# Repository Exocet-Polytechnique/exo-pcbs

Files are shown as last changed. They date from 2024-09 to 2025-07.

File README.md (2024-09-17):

# exo-pcbs
KiCad projects for our electrical control unit PCBs

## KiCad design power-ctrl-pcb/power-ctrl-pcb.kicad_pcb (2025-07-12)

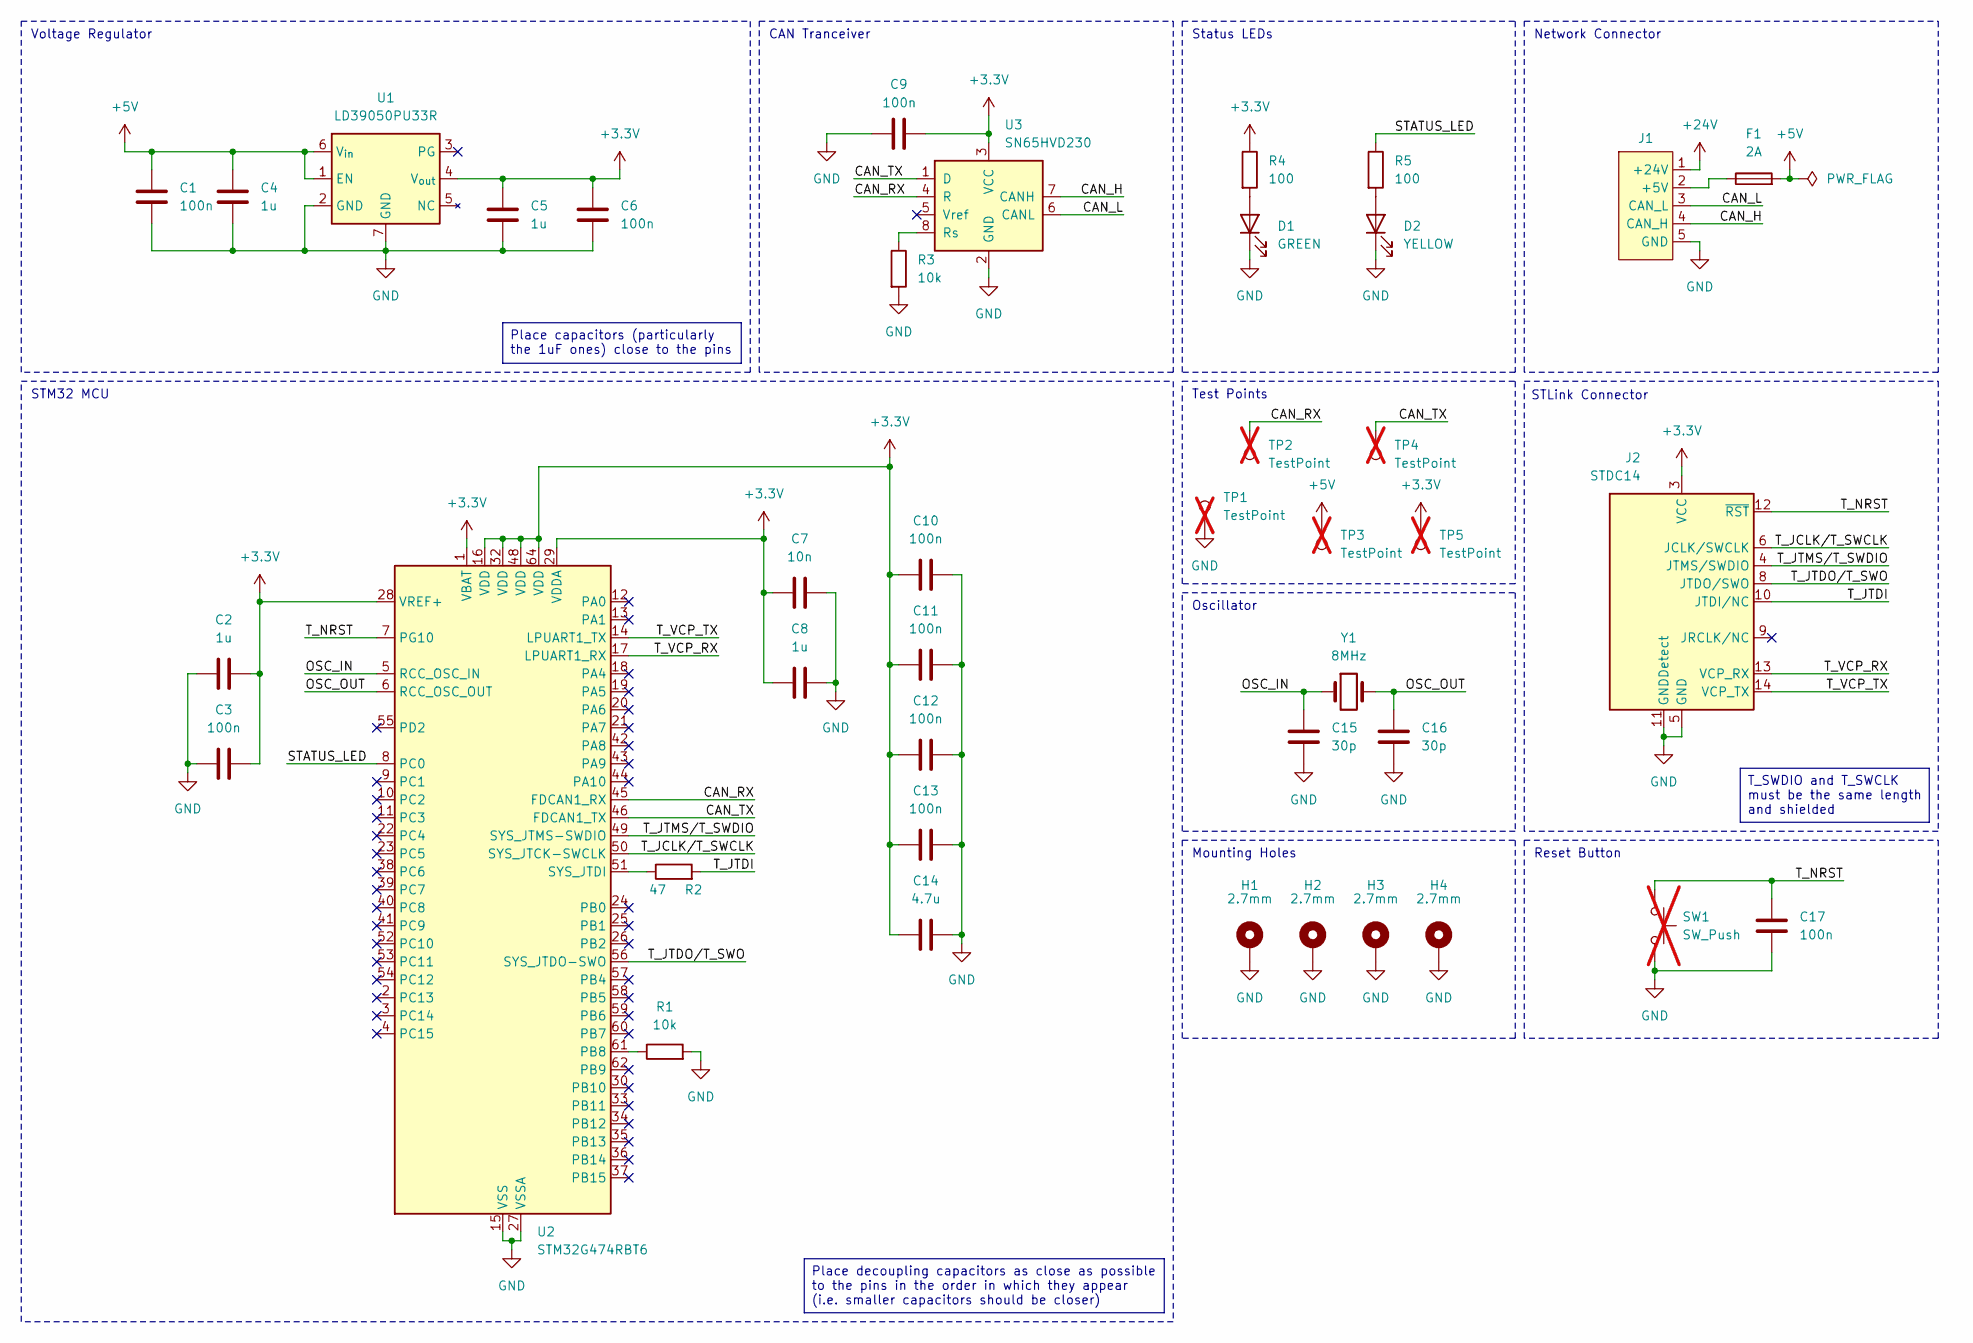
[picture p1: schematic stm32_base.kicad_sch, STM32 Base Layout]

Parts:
C1, C3, C6, C9, C10, C11, C12, C13, C17: 100n; C_0402_1005Metric; JLCPCB C1525
C2, C4, C5, C8: 1u; C_0402_1005Metric; JLCPCB C52923
C7: 10n; C_0402_1005Metric; JLCPCB C15195
C14: 4.7u; C_0402_1005Metric; JLCPCB C23733
C15, C16: 30p; C_0603_1608Metric; JLCPCB C1658
D1: GREEN; LED_0805_2012Metric_With_Annotations; JLCPCB C2297
D2: YELLOW; LED_0805_2012Metric_With_Annotations; JLCPCB C2296
F1: 2A; Fuse_Holder_Littelfuse_01530008; JLCPCB C206907
H1, H2, H3, H4: 2.7mm; MountingHole_2.7mm_Pad
J1: Network Connector; Molex_SPOX_5268-05A_1x05_P2.50mm_Horizontal; JLCPCB C185201
J2: STDC14; PinHeader_2x07_P1.27mm_Vertical_SMD; JLCPCB C7465995
R1, R3: 10k; R_0402_1005Metric; JLCPCB C25744
R2: 47; R_0603_1608Metric; JLCPCB C23182
R4, R5: 100; R_0402_1005Metric; JLCPCB C25076
SW1: SW_Push; SW_PUSH_6mm; not fitted
TP1, TP2, TP3, TP4, TP5: TestPoint; TestPoint_Keystone_5005-5009_Compact; not fitted
U1: LD39050PU33R; DFN-6-1EP_3x3mm_P0.95mm_EP1.7x2.6mm; JLCPCB C132827
U2: STM32G474RBT6; LQFP-64_10x10mm_P0.5mm; JLCPCB C529413
U3: SN65HVD230; SOIC-8_3.9x4.9mm_P1.27mm; JLCPCB C12084
Y1: 8MHz; Crystal_SMD_HC49-SD; Part Name X49SM8MSD2SC; JLCPCB C12674

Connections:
+3.3V: C2.2, C3.2, C5.1, C6.1, C7.1, C8.1, C9.1, C10.1, C11.1, C12.1, C13.1, C14.1, J2.3 (VCC), R4.1, TP5.1, U1.4 (V_{out}), U2.1 (VBAT), U2.16 (VDD), U2.28 (VREF+), U2.29 (VDDA), U2.32 (VDD), U2.48 (VDD), U2.64 (VDD), U3.3 (VCC)
+5V: C1.1, C4.1, F1.2, TP3.1, U1.1 (EN), U1.6 (V_{in})
+24V: J1.1 (+24V)
/STM32 Base Layout/CAN_H: J1.4 (CAN_H), U3.7 (CANH)
/STM32 Base Layout/CAN_L: J1.3 (CAN_L), U3.6 (CANL)
/STM32 Base Layout/CAN_RX: TP2.1, U2.45 (FDCAN1_RX), U3.4 (R)
/STM32 Base Layout/CAN_TX: TP4.1, U2.46 (FDCAN1_TX), U3.1 (D)
/STM32 Base Layout/OSC_IN: C15.1, U2.5 (RCC_OSC_IN), Y1.1
/STM32 Base Layout/OSC_OUT: C16.1, U2.6 (RCC_OSC_OUT), Y1.2
/STM32 Base Layout/STATUS_LED: R5.1, U2.8 (PC0)
/STM32 Base Layout/T_JCLK/T_SWCLK: J2.6 (JCLK/SWCLK), U2.50 (SYS_JTCK-SWCLK)
/STM32 Base Layout/T_JTDI: J2.10 (JTDI/NC), R2.2
/STM32 Base Layout/T_JTDO/T_SWO: J2.8 (JTDO/SWO), U2.56 (SYS_JTDO-SWO)
/STM32 Base Layout/T_JTMS/T_SWDIO: J2.4 (JTMS/SWDIO), U2.49 (SYS_JTMS-SWDIO)
/STM32 Base Layout/T_NRST: C17.2, J2.12 (~RST), SW1.1, U2.7 (PG10)
/STM32 Base Layout/T_VCP_RX: J2.13 (VCP_RX), U2.17 (LPUART1_RX)
/STM32 Base Layout/T_VCP_TX: J2.14 (VCP_TX), U2.14 (LPUART1_TX)
GND: C1.2, C2.1, C3.1, C4.2, C5.2, C6.2, C7.2, C8.2, C9.2, C10.2, C11.2, C12.2, C13.2, C14.2, C15.2, C16.2, C17.1, D1.1 (K), D2.1 (K), H1.1, H2.1, H3.1, H4.1, J1.5 (GND), J2.5 (GND), J2.7 (GND), J2.11 (GNDDetect), R1.2, R3.2, SW1.2, TP1.1, U1.2 (GND), U1.7 (GND), U2.15 (VSS), U2.27 (VSSA), U2.31 (VSS), U2.47 (VSS), U2.63 (VSS), U3.2 (GND)
unnamed: D1.2 (A), R4.2
unnamed: D2.2 (A), R5.2
unnamed: F1.1, J1.2 (+5V)
unnamed: R2.1, U2.51 (SYS_JTDI)
unnamed: R1.1, U2.61 (PB8)
unnamed: R3.1, U3.8 (Rs)

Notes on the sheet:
Oscillator
Reset Button
Mounting Holes
Voltage Regulator
CAN Tranceiver
Status LEDs
STLink Connector
Test Points
Network Connector
STM32 MCU
T_SWDIO and T_SWCLK must be the same length and shielded
Place capacitors (particularly the 1uF ones) close to the pins
Place decoupling capacitors as close as possible to the pins in the order in which they appear (i.e. smaller capacitors should be closer)

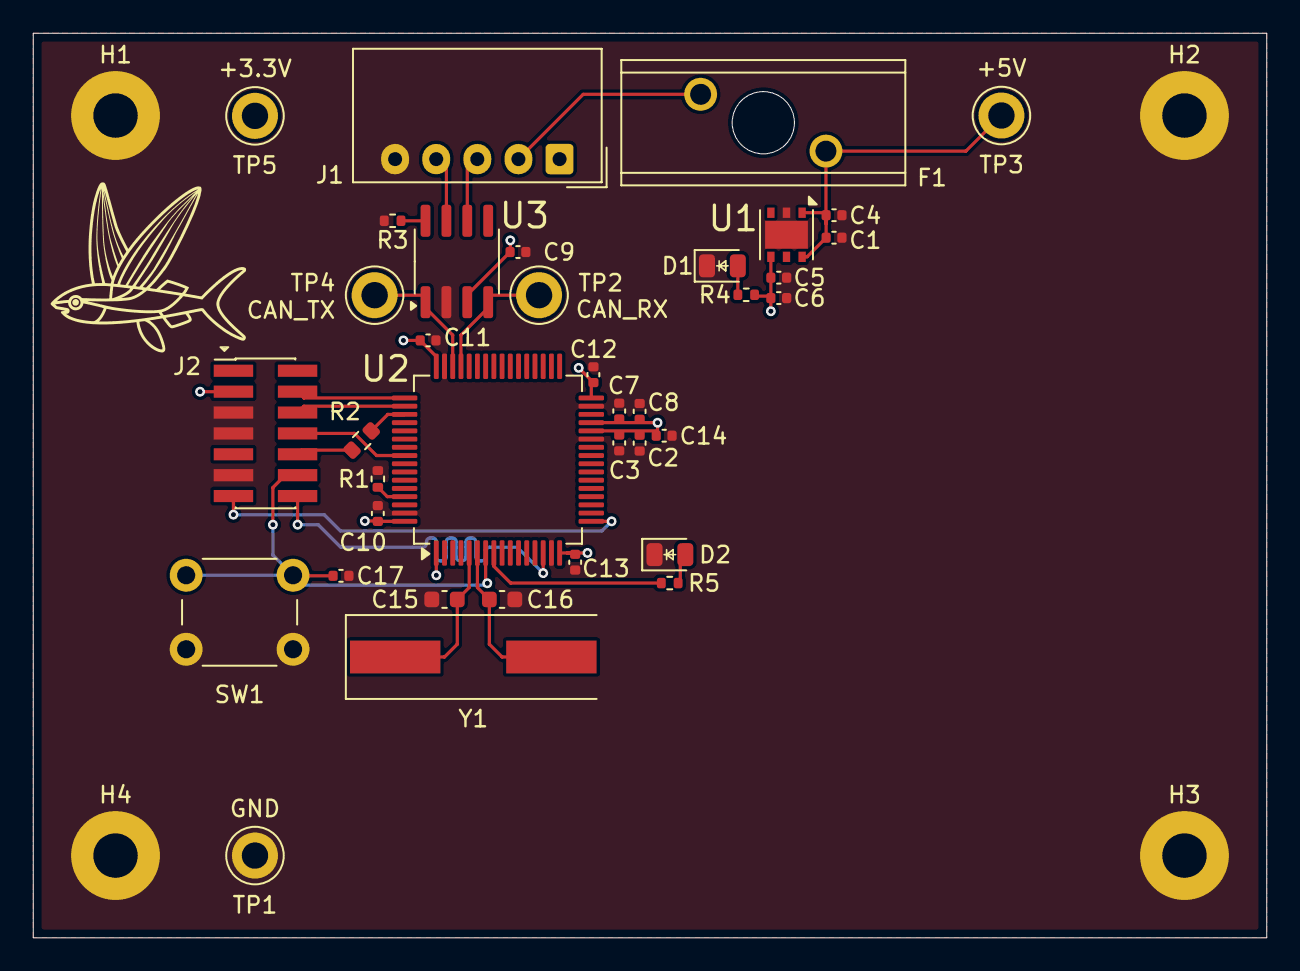
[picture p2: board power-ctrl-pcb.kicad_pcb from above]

Board: 2 copper layers, 75.0 x 55.0 mm, 41 parts (0 on the bottom side), 23 nets.

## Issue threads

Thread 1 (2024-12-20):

Faire le choix des pièces pour le template

efondere, 2024-12-20:
- [ ] Alimentation (incluant un *Volage Divider* et une diode Zener)
- [x] STM32G474RBT6 (et régulation de l'alimentation)
- [ ] Connexion pour la programmation
- [x] TJA1050T (CAN Tranceiver)
- [ ] Connecteur pour réseau CAN
- [x] X49SM8MSD2SC (Oscillateur pour bus CAN; à déterminer)
- [ ] Fusible(s)
- [x] 1 DEL par périphérique connecté
- [x] 1 DEL pour l'état du STM32
- [x] 1 DEL pour l'alimentation
- [ ] Switch et multiplexeur pour programmation (si nécessaire)
- [ ] Bouton pour reset la flash (à déterminer)
- [ ] Bouton pour reset le programme (à déterminer)

Closed 2025-04-09.

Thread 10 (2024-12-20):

PCB07 - DC-DC

efondere, 2024-12-20:
### Pièces à trouver
- [ ] 2 relais pour contacteurs
- [ ] Connecteur vers réseau CAN pour DC-DC
- [ ] Convertisseur 24V à 12V

efondere, 2025-06-28:
Sera inclu dans le PCB de contrôle de la haute puissance

Closed 2025-06-28.

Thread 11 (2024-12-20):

PCB08 - Contrôle haute puissance

efondere, 2024-12-20:
### Pièces à trouver
- [ ] 1 entrée GPIO (DMS)
- [ ] 1 relai pour contacteur (connecté directement au DMS)

**Attention** les requis pour ce PCB risquent de changer énormément dans les semaines/mois à venir

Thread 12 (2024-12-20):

HAT01 - Écran (Raspberry Pi)

efondere, 2024-12-20:
Bien qu'il existe des hats pré-existants pour ajouter une communication CAN à un raspberry pi, créer le notre nous donnera plus de flexibilité et nous permettra d'ajouter d'autres composantes (ex. pour l'alimentation)

### Pièces à trouver
- [ ] Connecteur GPIO RPi
- [ ] Alimentation RPi
- [x] MCP2515T-I (CAN controller)
- [x] TJA1050T (CAN tranceiver)
- [x] X49SM8MSD2SC (Oscillateur pour bus CAN)
- [ ] Connecteur vers réseau CAN

Nous avons fait un hat pour le Pi l'an dernier, donc on peut s'en inspirer pour cette année. Par contre, nous avons remarqué de grands problèmes avec la dissipation de chaleur, donc il faudrait trouver une solution pour ça (ex. faire un trou au milieur du PCB)

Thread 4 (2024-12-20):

Faire le schéma du template commun à tous nos PCBs

efondere, 2024-12-20:
Faire sur une feuille séparée et inclure la cartouche du template dans [`exo-electrical`](https://github.com/Exocet-Polytechnique/exo-electrical/tree/main/template).

Aussi, on pourra ajouter un `.html` et un `.png` pour les méta-données du template.

Closed 2025-04-09.

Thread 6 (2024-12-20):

PCB01 - Cockpit

efondere, 2024-12-20:
### Pièces à trouver
- [x] 2 types de connecteurs 2-pin (ex. JST, mais pas JST-PH)

_Voir avec moi ou @gumile pour la création du projet et l'organisation dans le dépôt git_

Closed 2025-04-09.

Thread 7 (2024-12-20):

PCB02 et PCB03 - Contrôleurs de Fuel Cell

efondere, 2024-12-20:
### Pièces à trouver
- [ ] 1 relai (vois plus si precharge nécessaire)
- [ ] Entrée pour câbles des contrôleurs de FC (USB ou UART - à déterminer)
- [ ] Connecteur pour capteur de température (**ATTENTION**: doit être le même que sur tous les autres PCBs; je metterai la _issue_ à jour quand on aura décidé)

efondere, 2025-06-28:
Sera inclu dans le PCB de contrôle de puissance

Closed 2025-06-28.

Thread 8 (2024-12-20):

PCB04 et PCB05 - Batteries

efondere, 2024-12-20:
### Pièces à trouver
- [x] LTC2944 (*battery gauge*)
- [ ] Connecteur pour capteur de température (voir #7 )
- [ ] EEPROM ou autre forme de mémoire morte effaçable
- [ ] Relai pour couper la batterie (test sans *LOAD* / *Open Circuit Voltage*)
- [ ] Résistance *shunt*
- [ ] Connecteur pour fils de la batterie (*ring terminal* ou *log terminal*)

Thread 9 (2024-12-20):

PCB06 - Plaque Hydrogène

efondere, 2024-12-20:
### Pièces à trouver
- [ ] 2 connecteur pour manomètres (3 pins)
- [ ] 2 relais pour les actuateurs des valves
- [ ] 2 connecteurs pour les actuateurs des valves (6 pins)
- [ ] 2 connecteurs pour capteur de température (voir #7 )

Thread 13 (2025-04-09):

CON01 - PCB de connexion générique

efondere, 2025-04-09:
Ce PCB sera conçu pour être versatile afin qu'il soit réutilisable pour plusieurs choses:
1. Connecter les PCB à l'intérieur des boîtiers;
2. Lire le bus CAN sur un ordi à l'aide du [PCAN](https://www.peak-system.com/PCAN-USB.199.0.html?L=1);
3. Connecter le DC-DC pour le configurer avec un ordi (voir point 2);
4. Pouvoir lire les signaux facilement à l'aide de test points (tensions, GND, CAN_H, CAN_L);
5. Pouvoir alimenter le bus par des sources de tensoins externe à travers des screw terminals.

De plus, il faudrait ajouter un [dip switch](https://en.wikipedia.org/wiki/DIP_switch) pour:
- Connecter ou non les résistances de terminaison du bus CAN (2 résistances de 120ohm, chacune indépendante)
- Alimenter ou non la pin "n_wakeup" du DC-DC

Il faut des traces pour les signaux ou tensions suivants:
- GND (plan)
- +5V (plan)
- +24V (trace plus large idéalement)
- +12V
- CAN_H
- CAN_L
- n_wakeup (juste pour le DC-DC)

Ainsi il faudra placer les composants suivants:
- 1 dip switch avec minimum 3 connexions (2x résistance + n_wakeup)
- 2 résistances de 120ohm entre CAN_H et CAN_L (à travers le dip switch)
- 4 à 5 connecteurs MOLEX SPOX (GND, CAN_H, CAN_L, +24V, +5V) (⚠ doit être dans le même ordre que [le template](https://github.com/Exocet-Polytechnique/exo-pcbs/tree/cockpit-pcb/template))
- 6 screw terminals (pour tous les signaux/tensions sauf n_wakeup)
- 6 test points (1/signal ou tension, sauf n_wakeup)
- 1 D-SUB à 9 pin pour le PCAN (voir "technical specifications" de la page du [PCAN](https://www.peak-system.com/PCAN-USB.199.0.html?L=1))
- 1 connecteur à 6 pin pour le DC-DC (voir p. 11 de la doc sur teams) -> pourrait être screw terminal ou autre

Pour le DC-DC, il faut brancher un signal n_wakeup qu'on contrôle avec le dip swich et pull-up ou pull-down avec la tension 12V. Ensuite, power supply sera branché au 12V aussi. La tension de 12V est utilisée pour le DC-DC seulemement. Le reste, soit les 2 GND et les signaux CAN_H, CAN_L se branchent aux même signaux sur le PCB.

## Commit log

2025-06-14 STLink connection schematic + AVX connector footprint
    [template.kicad_pcb, template.kicad_sch]
2025-06-14 Schematics for the first version of the STM32 template
    [template.kicad_sch]
2025-06-14 Add oscillator symbol
    [template.kicad_sch]
2025-06-14 Footprints and part numbers
    [template.kicad_sch]
2025-06-14 Initial placement and routing
    [template.kicad_pcb, template.kicad_sch]
2025-06-14 Routing done
    [template.kicad_pcb, template.kicad_sch]
2025-06-14 Move schematic to second page
    [stm32_base.kicad_sch, template.kicad_pcb, template.kicad_sch]
2025-06-14 Add license to drawing sheet template
    [template.kicad_pcb, template.kicad_sch]
2025-06-14 Add Exocet logo
    [template.kicad_pcb]
2025-06-14 Change B2B connector to STDC14 connector
    [stm32_base.kicad_sch, template.kicad_pcb]
2025-06-14 Connect BOOT0 to GND through 10k resistor
    [stm32_base.kicad_sch, template.kicad_pcb]
2025-06-14 Remove Termination Resistor (CAN Network)
    [stm32_base.kicad_sch]
2025-06-14 Assing JLCPCB Part Number
    [stm32_base.kicad_sch]
2025-06-14 Remove CAN Resistor and change the values of the LED resistors
    [stm32_base.kicad_sch, template.kicad_pcb]
2025-06-14 Correct Exocet logo
    [template.kicad_pcb]
2025-06-14 template: remove author email from drawing sheet
    [stm32_base.kicad_sch, template.kicad_pcb, template.kicad_sch]
2025-06-14 template: reorganize schematic for better fit
    [stm32_base.kicad_sch]
2025-06-14 template: move logo and change layer
    Logo is now in the top left, smaller and on the silkscreen layer
    [template.kicad_pcb]
2025-06-14 template: add triangle to indicate first pin of STDC14 STLink connector
    [template.kicad_pcb]
2025-06-14 template: rearrange traces near STDC14 STLink connector
    [template.kicad_pcb]
2025-06-14 template: change JLCPCB parts (capacitors & resistors)
    [stm32_base.kicad_sch]
2025-06-14 template: parts placement optimisation
    [template.kicad_pcb]
2025-06-14 template: labels, traces, & parts placement corrections
    [template.kicad_pcb]
2025-06-14 template: re-reference all components
    Had to re-add R1 and J2, but they were replaced where they were.
    [stm32_base.kicad_sch, template.kicad_pcb]
2025-06-14 template: rotate R1 reference label
    Make it horizontal like all the others
    [template.kicad_pcb]
2025-07-12 power-ctrl-pcb: initial project files
    [power-ctrl-pcb.kicad_pcb, power-ctrl-pcb.kicad_sch, stm32_base.kicad_sch]
